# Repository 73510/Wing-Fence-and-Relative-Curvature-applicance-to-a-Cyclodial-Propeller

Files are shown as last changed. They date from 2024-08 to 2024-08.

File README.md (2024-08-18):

# Wing Fence and Relative Curvature applicance to a Cyclodial Propeller🚁
 사이클로디얼 프로펠러에 윙펜스와 상대 곡률 이론 적용시 일어나는 성능 변화를 실험적으로 검토했습니다.

## 📚 프로젝트 개요

이 저장소는 사이클로디얼 프로펠러의 성능을 개선하기 위한 연구를 담고 있습니다. 프로젝트는 여러 버전을 거쳐 발전했으며, 각 버전은 다양한 측면과 대회에 초점을 맞추었습니다.

## 🗂 저장소 구조

```
├─BUILD
│  ├─V0_V1_BUILD
│  └─V2_V3_BUILD
├─대회 출전 Documentation
│  ├─V0_교내과제연구
│  ├─V1_서울과학전람회예선
│  ├─V2_삼성휴먼테크논문대상
│  └─V3_KSEF CYC
└─데이터 및 실험 설계
    ├─Codes
    └─rawdata
```

## 🔬 연구 진행 과정

### V0: 교내 과제 연구
- Wing Fence와 Relative Curvature 개념 도입
- CFD(Computational Fluid Dynamics) 시뮬레이션 수행
#### 1차 모델 실험



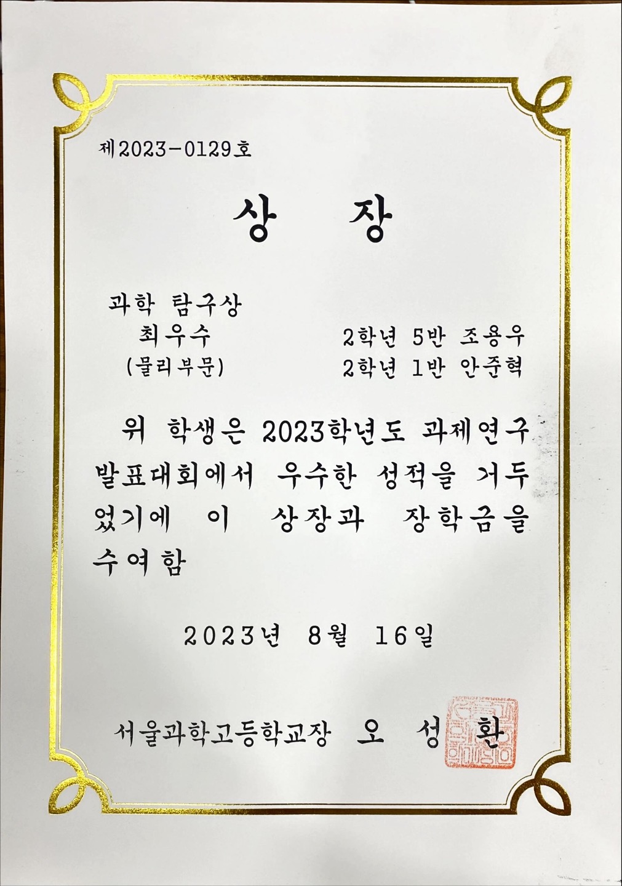
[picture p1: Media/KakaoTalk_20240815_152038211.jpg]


### V1: 서울과학전람회 예선 최우수상
- 프로펠러 설계 개선
- 논문 개선 및 수정



### V2: 삼성휴먼테크논문대상
- 최종 프로토타입 제작 및 성능 테스트
- Variable Pitcher 설계로 Pitch Distance 조절 가능
- 다양한 측정 도구를 활용한 종합적인 성능 분석 (RPM, 소음, 전력 소비량 등)

- 초록 통과, 본선 탈락
#### 2차 모델
- 기존의 3D 출력 날개가 무거워 폼보드 적용 경량화
- 부품 최소화시키고 프레임을 카본파이버로 구성
- 맞물린 기어 대신 풀리와 벨트 사용
- 하지만 폼보드 가공 문제에 부딫혀 3D 프린터로 만들게 됨

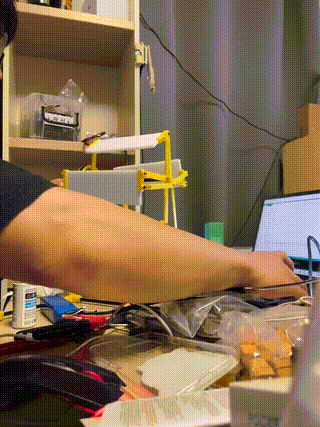
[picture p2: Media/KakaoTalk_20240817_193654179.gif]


#### 3차 모델
- NACA 0012 단면 형상 적용 날개
- Flaparm 내구도 문제 제외 완벽했다 -> 최종 모델에서 개선
- 2차 모델에 비하여 약간의 무게가 증가한 것이 단점

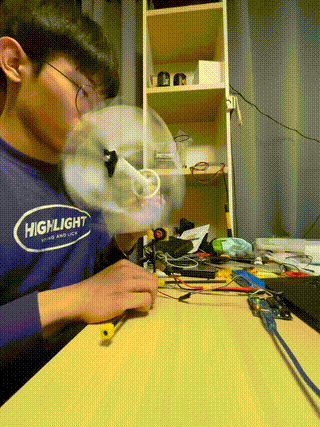
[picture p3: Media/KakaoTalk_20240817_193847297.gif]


#### 최종 모델 : 
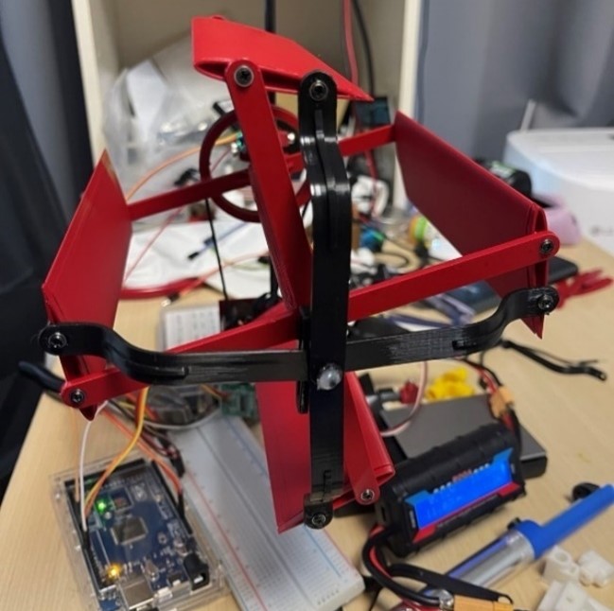
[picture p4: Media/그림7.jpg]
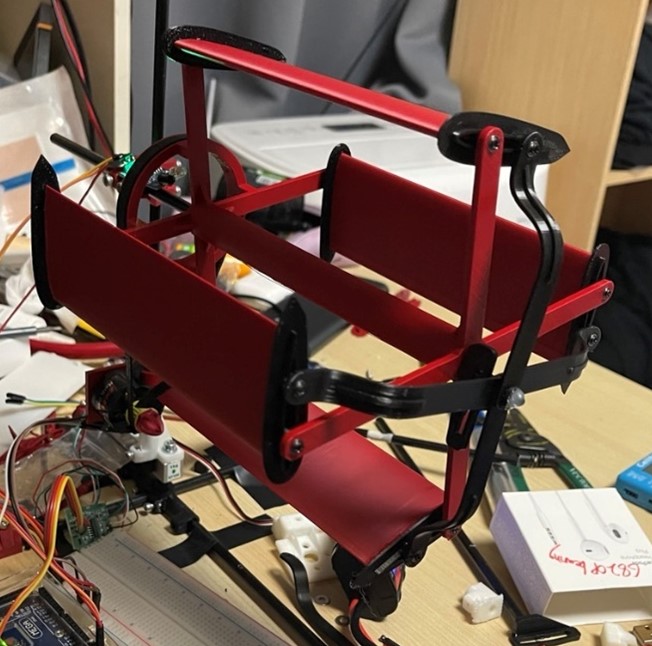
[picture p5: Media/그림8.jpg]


### V3: KSEF (Korea Science & Engineering Fair)
- 경량화 모델 LW-PLA 적용 실험
- 기존 프로펠러와의 성능 비교 분석
- 기존 프로펠러 실험 영상
  
  **Arduino Serial Monitor Loadcell & Tachometer RPM value**

- 최종 보고서 작성 및 개선

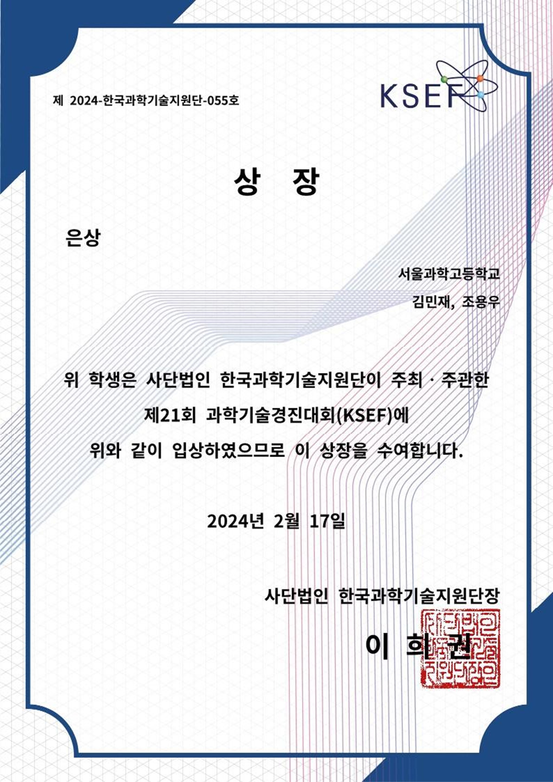
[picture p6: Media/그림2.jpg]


## 🛠 주요 연구 내용

1. [**프로펠러 설계 및 제작**](./BUILD/)
   - 3D 모델링 및 프린팅 (BUILD 폴더 참조)
   - 다양한 에어포일 설계 실험

2. [**성능 측정 및 분석**](./데이터%20및%20실험%20설계/)
   - Arduino를 이용한 데이터 수집
   - Python을 이용한 데이터 분석 및 시각화

3. [**Wing Fence 및 Relative Curvature 연구**](./대회%20출전%20Documentation/)
   - 이론적 배경 및 적용
   - 실험과 CFD를 통한 효과 검증

4. [**경량화 연구**](./대회%20출전%20Documentation/V3_KSEF%20CYC/)
   - LW PLA 활용 실험
   - 강성 유지와 경량화 사이의 균형점 모색

## 📊 데이터 및 결과

- 실험 원시 데이터: [`rawdata`](./데이터%20및%20실험%20설계/rawdata/) 폴더
- 데이터 분석 결과: [`데이터 및 실험 설계`](./데이터%20및%20실험%20설계/) 폴더
- 최종 연구 결과: [`대회 출전 Documentation/V3_KSEF CYC`](./대회%20출전%20Documentation/V3_KSEF%20CYC/) 폴더

## 🔮 향후 연구 방향

- 더욱 효율적인 에어포일 설계 탐구
- 다양한 소재를 활용한 경량화 연구 지속
- 실제 비행체 적용을 위한 스케일업 연구

## 📧 연락처

프로젝트에 대해 궁금한 점이 있으시면 언제든 연락 주세요!

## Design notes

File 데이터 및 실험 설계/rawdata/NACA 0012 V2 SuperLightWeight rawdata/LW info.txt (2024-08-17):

원래 PLA Not Curved WF Assemble

Main144 + L Wf + R WF + insert x3 = 17.4g

LightWeight Version -> 6.5g으로 경량화.

Setting
flowrate 0.4에 (0.41~0.42는 되야 함)Layer height 0.3, width 0.6에 Vase mode

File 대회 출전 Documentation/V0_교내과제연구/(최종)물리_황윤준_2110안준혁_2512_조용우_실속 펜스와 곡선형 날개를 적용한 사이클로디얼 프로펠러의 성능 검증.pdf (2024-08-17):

- 1 -

## 실속 펜스와 곡선형 날개를 적용한 사이클로디얼 프로펠러의 성능 검증

안준혁 ․ 조용우 ․ 황윤준
서울과학고등학교

### Wing Fence & Curved Wing Effect on Cyclodial Propellers

JunHyuk Ahn ․ Yongwoo Cho ․ Yunjun Hwang Seoul Science High School

### 국문 초록

본 연구에서는 Cycloidal Propeller의 효율 개선을 위해 Wing Fence 구조와 Virtual Camber 효과를 고려한 날개

형상을 적용하는 방안을 모색하였다. Cycloidal Propeller는 회전축이 유체의 이동 방향에 수직인 유체 추진 장치

로, 항공 및 수상 차량의 추진, 상승, 조종에 사용된다. 그러나 기존의 Cycloidal Propeller는 상대 곡률에 의해 전

력 손실이 발생하는 문제가 있었다. 이에 본 연구에서는 공력학적 장치인 Wing Fence의 원리를 도입하여 안정성

및 추력을 향상시키고, Relative Curvature 형상을 최적화하여 전력 손실을 줄이는 방안을 제시하였다. Computational Fluid Mechanics를 이용한 실험 결과, 새로운 구조와 형상이 적용된 Cycloidal Propeller는 기존 대

비 효율 개선을 보였으며, 이는 향후 항공 및 수상 차량의 추진 시스템에 대한 새로운 접근 방법을 제공할 것으로
기대된다. | Abstract

In this study, we tried to improve the efficiency of a cyclic propeller by applying a wing fence structure and a wing shape that considers the virtual camber effect. A cyclic propeller is a fluid propulsion device whose rotational axis is perpendicular to the direction of fluid movement, and is used for propulsion, ascent, and control of air and water vehicles. However, conventional cyclonic propellers suffer from power loss due to relative curvature. In this study, we propose to improve stability and thrust by introducing the principle of wing fence, an aerodynamic device, and to reduce power loss by optimizing the relative curvature shape. As a result of experiments using Computational Fluid Mechanics, the Cyclloidal Propeller with the new structure and shape showed efficiency improvement compared to the existing one, which is expected to provide a new approach to the propulsion system of air and water vehicles in the future.

Keywords : Cyclodial Propeller, Wing Fence, Virtual Camber, Computational Fluid Mechanics, 효율 개선

### I. 서론(Introduction)

Cycloidal Propeller는 유체 추진 장치로, 항공 및 수상 차량의 추진, 상승, 조종에 중요한 역할을 수행한다. 이러

한 기기의 효율을 극대화하기 위해 다양한 노력이 지속적으로 이루어지고 있다. 그러나 기존의 Cycloidal Propeller

는 상대 곡률로 인해 전력 손실이 발생하는 문제를 안고 있다. 이러한 문제를 해결하고 Cycloidal Propeller의 성능

을 향상시키기 위한 연구가 시급하다. 이에, 본 연구에서는 공력학적 장치인 Wing Fence 구조와 Relative

Curvature 형상을 Cycloidal Propeller에 적용, 그 성능 향상을 추구하는 것이 목표이다.

- 2 -

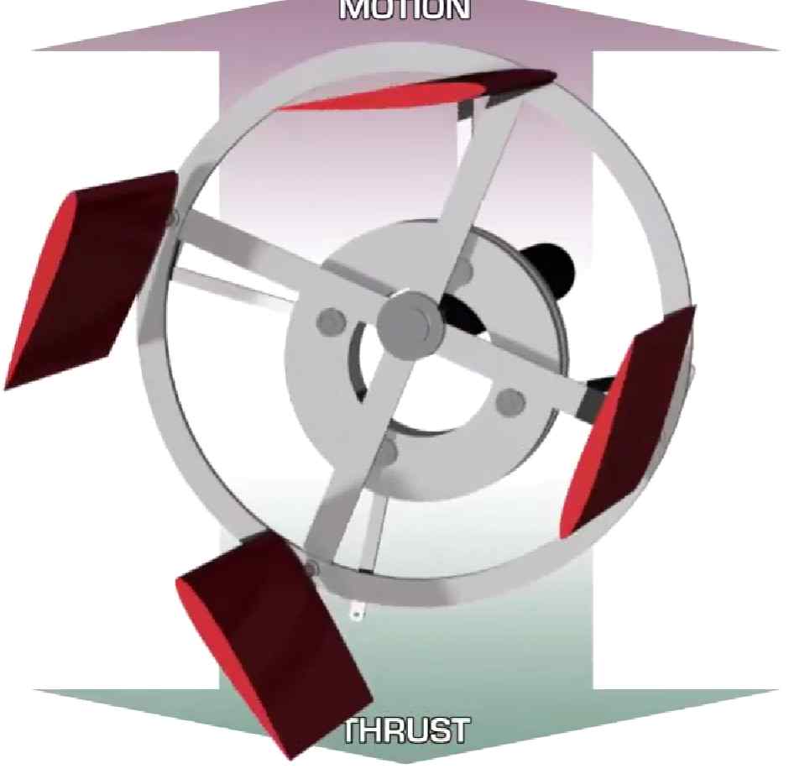
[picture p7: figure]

그림 1 : Cyclodial Propeller의 형상, 출처 https://youtu.be/Ub563Yc3xls. 축과 나란한 방향이 아닌, 축과 수직한 방향으로 추력이 발생하도록 회전한다. Flap이라는 구조가 회전하면서 추

력을 만들어내며, 기존 프로펠러와 달리 모든 면이 같은 속도로 공기와 만나 구조적으로 단순해진다는 장점이 존

재한다. Cycloidal Propeller와 관련된 이론과 선행 연구는 그 동작 원리와 구조, 그리고 성능 개선 방안 등에 집중되어

왔다. 특히, 이 장치의 추력 손실 문제를 해결하기 위한 다양한 접근법이 제시되었으나, 아직까지 뚜렷한 해결책은

마련되지 못하였다. 본 연구에서는 Wing Fence와 Relative Curvature라는 두 가지 새로운 개념을 도입한다. Wing Fence는 주로 스웹

트 날개(swept-wing) 항공기에 장착되며, 공기가 너무 멀리 이동하거나 속도가 빨라져 전체 날개가 한번에 기능을

상실하는 것을 방지하는 역할을 한다. 반면, Relative Curvature는 날개의 곡률을 조절하여 날개 주변의 유동을 최

적화하고 전력 손실을 줄이는 방식이다. 이 두 가지 개념을 Cycloidal Propeller에 적용하여 그 성능을 개선하고자

하는 것이 본 연구의 주요 동기이다. 스웹트 날개(swept-wing) 항공기가 저속으로 비행할 때, 날개의 전방 모서리 각도로 인해 일부 공기 흐름이 횡방향

으로, 즉 날개 끝쪽으로 이동하게 된다. 이 과정은 점진적으로 진행되며, 날개 중앙 부근의 공기 흐름은 전방 모서

리 각도뿐만 아니라 날개 뿌리로부터의 횡방향 공기 흐름에 영향을 받는다. 이로 인해 날개 끝에서는 공기 흐름이

거의 모두 횡방향으로 이동하게 되어, 이는 날개를 앞뒤로 가로지르는 흐름과 대조적이다. 이는 결과적으로 효과적

인 공기 속도가 크게 떨어져 날개가 고속 유동 상태에서 벗어나게 된다. 이런 문제를 해결하기 위해 'Wing Fence'의 도입이 필요하다. 'Wing Fence'는 공기 흐름이 너무 멀리 이동하거나

속도가 빨라져 전체 날개가 한번에 기능을 상실하는 것을 방지하는 역할을 한다. Cyclodial Propeller에서 또한, 날

개 양 끝단에서 발생하는 횡방향 모멘텀을 올바르게 제어하고 추진하기 위해서는 wing fence의 구조가 필요하다. 본 연구에서는 Cycloidal propeller의 성능 개선과 관련하여 다음 세 가설을 세우고, 이를 증명하기 위한 시뮬레

이션과 실험을 진행하였다. 가설 1. Cycloidal propeller의 회전 반경과 같은 곡률 반지름의 날개를 이용하면 drag를 감소시켜 효율을 높일

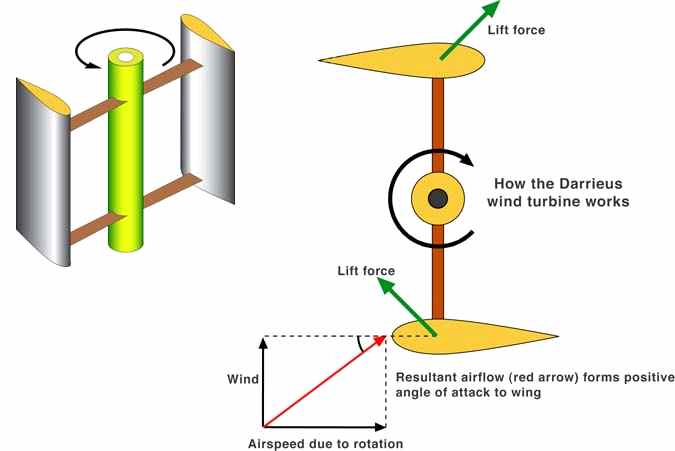
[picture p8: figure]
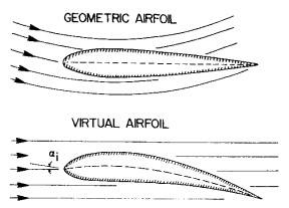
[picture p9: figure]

- 3 -

수 있다. 가설 2. Cycloidal propeller의 회전 반경과 같은 곡률 반지름의 날개를 이용하면 추력을 증가시킬 수 있다. 가설 3. Cycloidal propeller의 날개에 wing fence 구조를 설치하면 추력 개선 효과가 있다.

### II. 연구방법 및 이론(Method & Theory)

### 1. 가설에 대한 정성적인 근거

가설 1) P. G. Migliore의 ‘Flow Curvature Effects on Darrieus Turbine Blade Aerodynamics’에 따르면, Darrieus

turbine blade의 공기역학적 특성에는 유체 흐름의 곡률이 중요한 영향을 끼친다. Darrieus turbine은 cyclorotor와

마찬가지로 익형 구조의 날개를 어떤 축 주위로 회전할 수 있도록 하는 풍력 발전기이다. 이때 각각의 날개는 곡선

운동을 하게 되는데, 이 때문에 실제보다 캠버(camber)가 큰 (익형의 휘어진 정도가 큰) 효과가 발생한다고 한다. 이를 virtual camber effect라 한다. 해당 논문에서는 이를 conformal mapping technique를 이용하여 표현한다. 또

한 virtual camber effect의 conformal mapping을 나타낸 아래 그림에서 알 수 있듯 받음각(Angle of Attack, AoA)

이 증가하는 효과도 있다.

그림 2 : Darrieus turbine의 작동 원리

그림 3 : Curvilinear flow에 대해 conformal mapping

을 적용한 virtual airfoil 주의의 rectilinear flow

Cycloidal propeller의 회전 반경과 같은 곡률 반지름의 날개를 이용할 경우, 날개 주위의 유속이 rectilinear flow

의 모양을 따르도록 conformal mapping을 하면 angle of attack이 0인 상황과 대응되며, drag force가 최소이다. 따

라서 날개가 지면과 수직인 방향으로 이동할 때도 virtual camber effect에 의해 drag가 생성되는 편평한 날개에 비

해 곡률 반지름이 날개의 회전 반경과 일치하는 날개가 에너지 관점에서 더 효율적일 것이다.

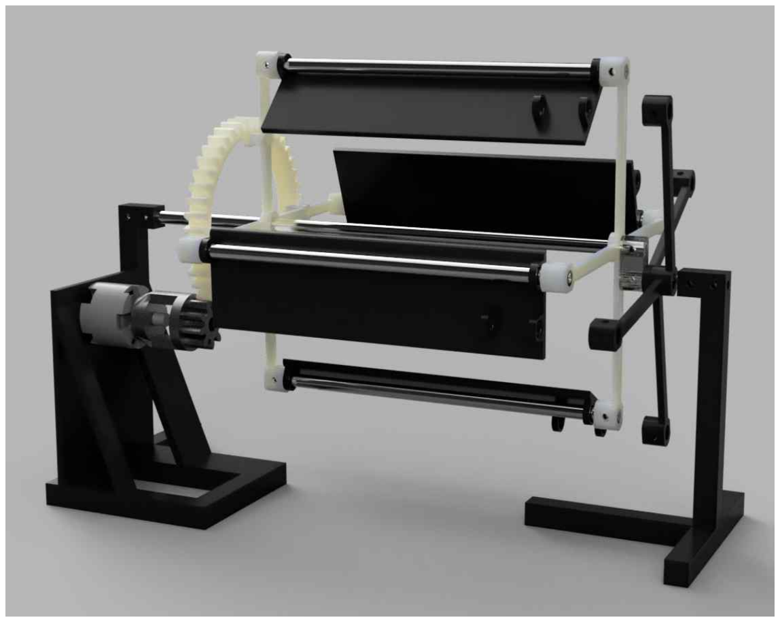
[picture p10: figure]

- 4 -

가설 2) 날개 자체가 휘어져 있으면 virtual camber effect 외에도 날개에 camber가 있는 효과가 있어 날개가

cycloidal propeller의 위, 아래쪽에 있을 때 받는 양력이 더 클 것이다. 가설 3) Swept-wing 항공기에 설치되는 wing fence와 마찬가지로, cycloidal propeller의 날개에 wing fence 유사

구조물을 설치하면 날개에 나란한 방향으로의 유체 흐름을 막아 날개에 수직한 방향의 운동량을 유지하는 효과가

있어 양력이 클 것이다.

2. 3D Printed Parts & Structure

연구를 진행하기 위해, Cyclodial Propeller를 3D 프린터로 만들었다. 이를 위해 아래 사진과 같이, 다양한 날개의 구조를 실험할 수 있는 Cyclodial Propeller를 제작하였다.

그림 4 : 전체 Cyclodial Propeller 실험 장치의 구성

다음은 각 부품에 대한 명칭 및 이름이다.

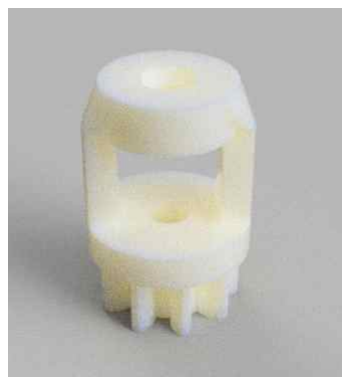
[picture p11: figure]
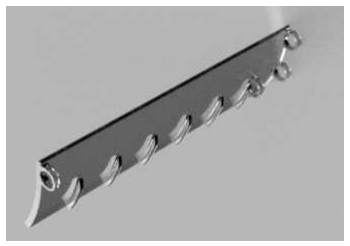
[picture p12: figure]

- 5 -

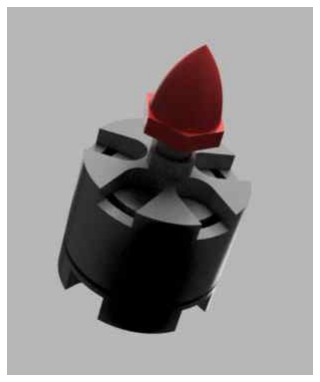
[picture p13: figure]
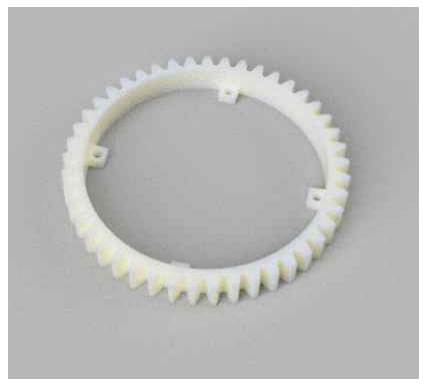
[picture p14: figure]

그림 5 : A : 45T Module 2 Gear. 큰 기어로 1/5의 비로 모터와 주회전축 로터를 연결한다. B : Real Gear 9. 모

터 마운트의 형상에 기초하여 모터에 쉽게 탈부착가능한 기어이다. 9T이다. 두 기어 모두 Fusion 360의 Spur Gear

를 사용했으며, 두께 10mm 에 Module 2로 설계하였다. C : MT2212 motor. 실험에 쓰이는 드론 모터로, 주로 멀

티콥터에 적용되는 모터이다. 프로토타입을 만들었을 때 2 : 1 의 비로 연결하였으나 작동하지 않아, 차후 5 : 1

의 기어비로 수정하였다.

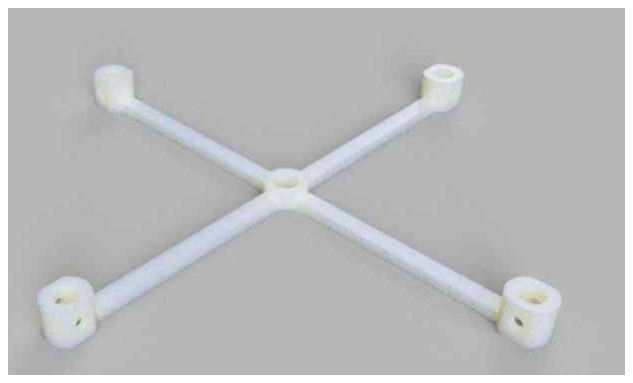
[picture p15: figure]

그림 6 : A : CenterArm. 주회전축의 날개 4개가 회전하는 것을 붙잡는 중앙 지지대이다. B : CenterArmGear.

기어를 마운트할 수 있는 스페이서와 구멍이 연결되어 있어 나사로 연결 할 수 있다. 마찬가지로, 주회전축의 날

개 4개 회전을 붙잡는 중앙 지지대이다. C : FlapArm. 날개의 각도가 유동적으로 제어되는데 있어 필수적인, 이

심축에 연결되어 날개의 각도를 제어하는 지지대이다. 이때, 각 Arm 사이에는 내경 4mm 외경 6mm 알루미늄

파이프로 연결된다. D : Pitch12mm. 이심축과 주회전축을 연결하는 연결 부위이다. 12mm의 간격을 두고 떨어

져 있다.

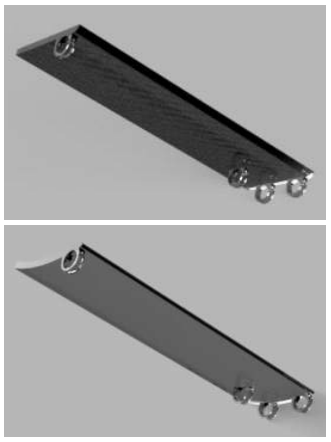
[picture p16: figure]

그림 8 : A : StraightFlap. B : StraightWF Flap. C : RoundFlap. D : RoundWF Flap.

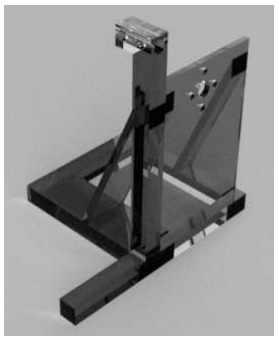
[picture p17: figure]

- 6 -

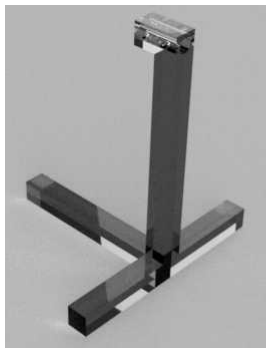
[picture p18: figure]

그림 9 : A : Stand. 회전축을 고정하기 위한 스탠드이다. 이심축이 두 개의 나사로 고정된다. B : StandMotorMount. 모터

마운트와 지지대가 포함된 스탠드이다. 모든 설계 자료는 “설계 자료” directory에 fusion 360 archive 형식으로 저장되어 있다.

### 3. 파이썬을 이용한 Flap Angle Distribution 찾기

Flap의 각도는 주회전축과 이심축 사이 거리, 날개의 반지름, Flap고정축간 거리에 의해 결정된다. 하지만 이 관

계가 비선형적이기 때문에, 파이썬을 이용해 각도 분배를 찾았다. 아래는 이를 찾기 위한 좌표평면상 좌표 정의이다.

- 7 -

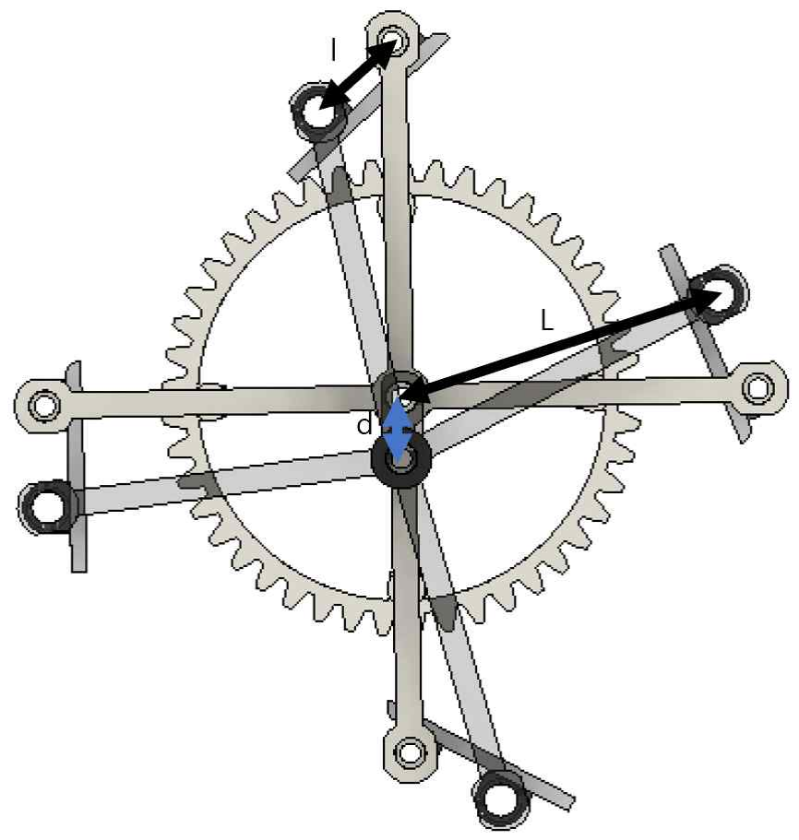
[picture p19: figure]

그림 10 : 회전축에 수직한 면에서 바라본 구조이다. l : Flap에서 두 고정축 간 거리 (두 축은 회전 가능함). 20mm로 설계되었다. L : 주회전축과 Flap이 고정되는 축 사이 거리. CenterArm과 FlapArm 모두 70mm 길이로 설계되었다. d : 주회전축과 이심축 간 거리, 본 설계에서는 12mm이다. Pitch Angle : Flap이 주회전축을 중심으로 하며 반지름이 L인 원의 접선과 이루는 각도. Theta : 좌표평면상 회전각, 0부터 2까지의 값을 가진다. 그래프에서는 x축이며, 편의를 위해 0~2까지의 값으로

scale down 하였다. 다음과 같이 값과 좌표를 설정한 이후, 파이썬을 이용한 수치대입법으로 해를 근사하여 구한 이후, 각도를 계산하

여 그래프를 그렸다. (첨부폴더 mechanicspy)

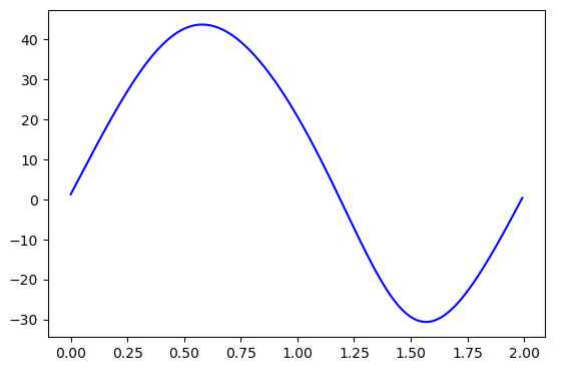
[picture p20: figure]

그림 11 : 그래프 y축은 도, x축은 theta/이다. A : d : 12mm, L : 70mm, l : 20mm의 설계. 최종 설계 버전의

각도 분배이며, 최댓값 43.7도, 최솟값 –30.6도의 값을 가진다. B : d : 10mm, L : 80mm, l : 20mm. 초기 설계이

며, 최댓값 36.4도, 최솟값 –24.0도의 값을 가진다. L의 증가는 최대각과 최소각의 절댓값 차이를 줄이는 역할을 하며, 위아래의 출력을 더 편평하게 맞추는데 기여

한다. d의 증가는 더 큰 Pitch Angle을 준다.

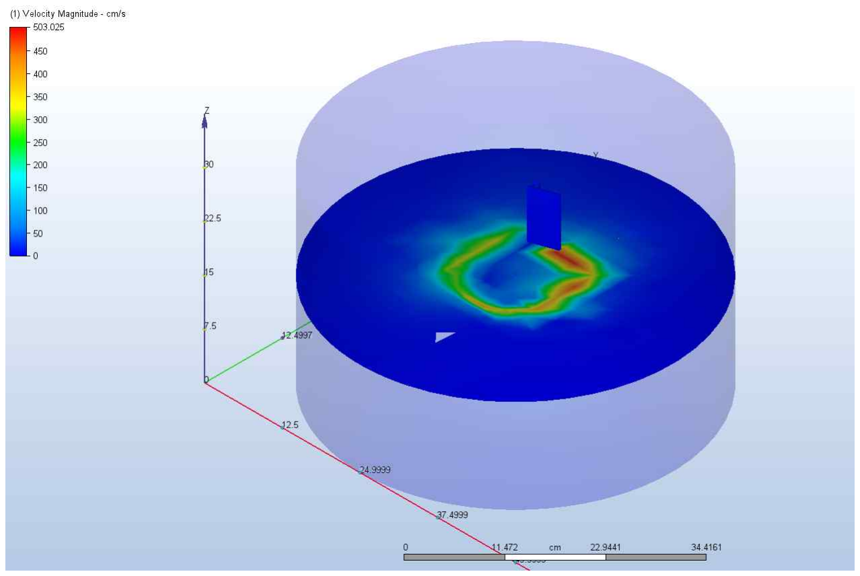
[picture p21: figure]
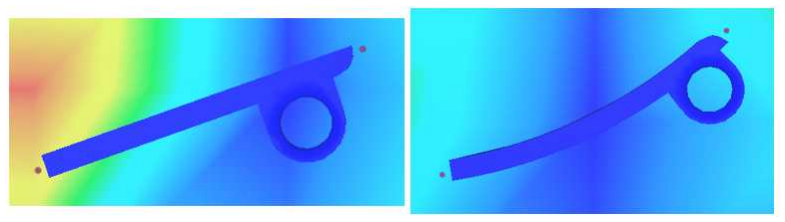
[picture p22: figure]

- 8 -

### 4. CFD 시뮬레이션을 이용한 가설 1 검증

Cycloidal propeller의 날개 구조에 따라 pitch angle이 0일 때 작용하는 drag force를 비교하기 위해 Autodesk

CFD를 이용한 시뮬레이션을 진행했다. 실제 실험 조건과 같이 지름 500mm인 영역의 중심을 기준으로 반지름

70mm인 원형 궤도를 따라 StraightFlap 또는 RoundFlap을 700 RPM으로 회전시켰다. 유체는 Air, 날개는

ABS(molded)로 설정했다.

그림 12 : StraightFlap 회전 시뮬레이션 이미지

총 100 step 동안 시뮬레이션을 작동시켰으며, 91~100 step에서 날개의 중심을 수직으로 관통하는 평면에서 아래

그림과 같이 날개의 진행방향을 기준으로 앞과 뒤 점의 압력을 측정했다.

그림 13 : A. StraightFlap 앞뒤 압력 측정점 / B. RoundFlap 앞뒤 압력 측정점

### 5. CFD 시뮬레이션을 이용한 가설 3 검증

Cycloidal propeller의 날개에 부착된 wing fence 구조의 효과를 이론적으로 확인해보기 위해 Autodesk CFD를

이용한 시뮬레이션을 진행했다. 10m/s의 rectilinear한 공기 흐름 속에서 StraightFlap과 StraightWF Flap을 각각

pitch angle이 0도, 15도인 경우에 대해 50 step 이후의 결과를 측정했다. 시뮬레이션 영역은 날개를 중심에 둔

300mm*200mm*500mm 크기의 직육면체이다. 유체는 Air, 날개는 ABS(molded)로 설정했다.

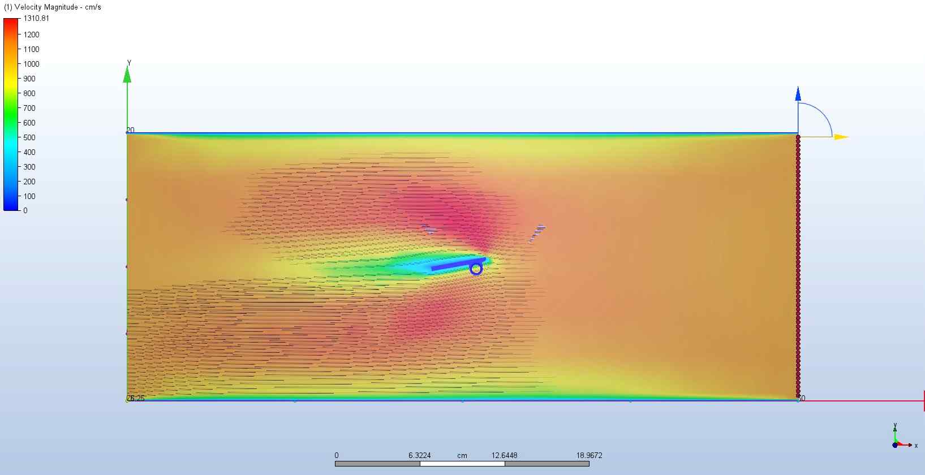
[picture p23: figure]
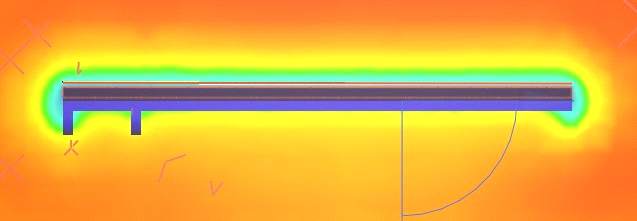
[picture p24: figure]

- 9 -

그림 14 : Pitch angle 이 15도인 StraightFlap 주위의 유체 흐름 단면도

50 step 정도에 공기의 흐름이 평형상태에 도달했다고 가정하고 날개를 관통하며 공기 흐름에 수직한 방향으로

자른 평면상에서 날개의 바로 위쪽의 직선을 따라 공기의 속력을 측정했다. 또한 이때 날개에 작용하는 x, y, z 방

향 힘을 측정했다.

그림 15 : 날개 위 속력이 비취색으로 표현된 영역의 붉은색 가로줄을 따라 속력 데이터를 측정했다.

6. 1차 실험

3D 프린터와 레이저 커터를 이용하여 부품을 출력한 후 아래 그림과 같이 1차 실험에 사용한 모델에 맞게 조립

하였다. 기존 설계상으로는 드론 모터를 이용하여 cycloidal propeller를 회전시키려 했으나 해당 설계상 기어비가

낮아 모터의 토크가 충분하지 않았다. 따라서 1차 실험에서는 드릴에 기어를 부착해 cycloidal propeller를 작동시켰

다. 회전 각속도를 알기 위해 타코미터를 사용했다. 아래 그림의 B와 같이 모델의 받침대 부분을 Force Plate 위에

고정시키고 Vernier Labquest를 이용하여 시간에 따른 힘 데이터를 측정했다. Cycloidal propeller를 Force Plate 위

에 설치하기 전에 Vernier Labquest로 영점 조절을 해야 한다.

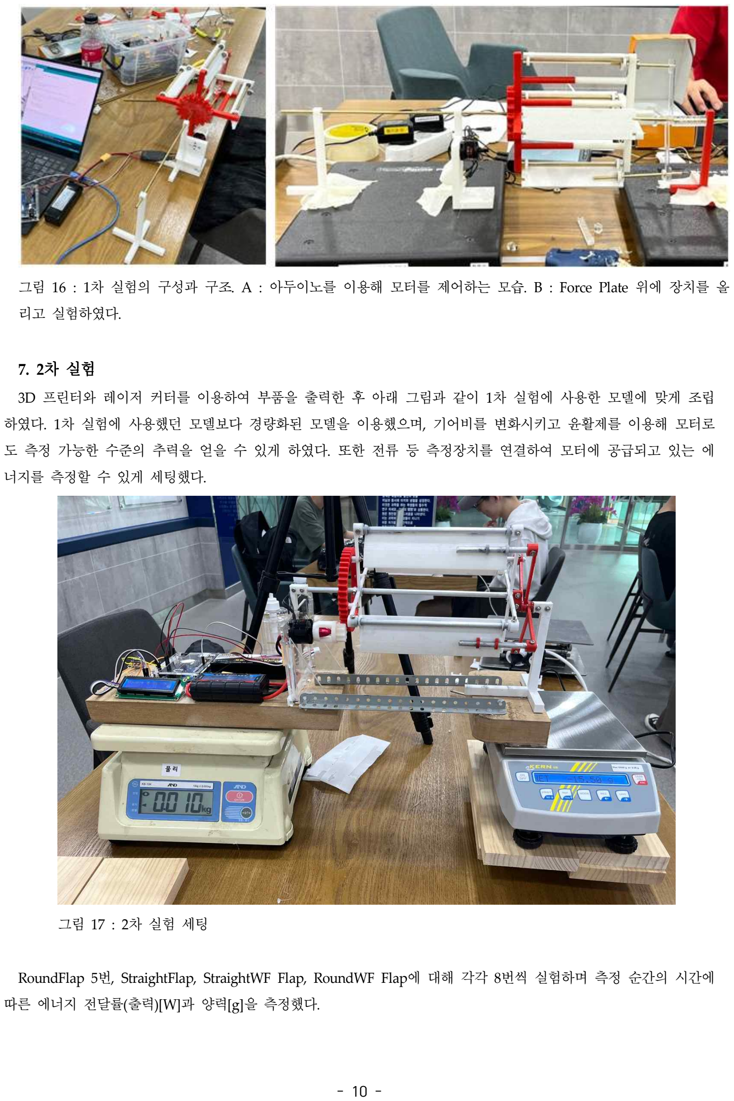
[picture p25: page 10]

- 10 -

그림 16 : 1차 실험의 구성과 구조. A : 아두이노를 이용해 모터를 제어하는 모습. B : Force Plate 위에 장치를 올

리고 실험하였다.

7. 2차 실험

3D 프린터와 레이저 커터를 이용하여 부품을 출력한 후 아래 그림과 같이 1차 실험에 사용한 모델에 맞게 조립

하였다. 1차 실험에 사용했던 모델보다 경량화된 모델을 이용했으며, 기어비를 변화시키고 윤활제를 이용해 모터로

도 측정 가능한 수준의 추력을 얻을 수 있게 하였다. 또한 전류 등 측정장치를 연결하여 모터에 공급되고 있는 에

너지를 측정할 수 있게 세팅했다.

그림 17 : 2차 실험 세팅

RoundFlap 5번, StraightFlap, StraightWF Flap, RoundWF Flap에 대해 각각 8번씩 실험하며 측정 순간의 시간에

따른 에너지 전달률(출력)[W]과 양력[g]을 측정했다.

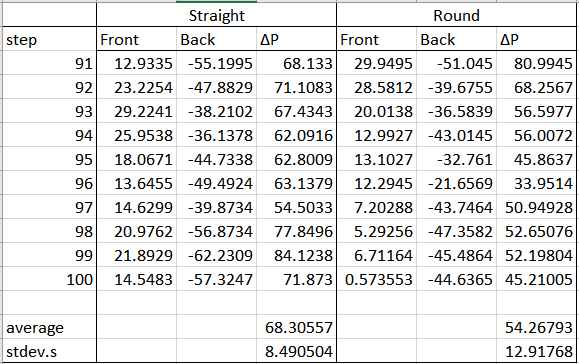
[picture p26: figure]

- 11 -

### III. 결과

### 1. 시뮬레이션 – 가설 1

다음 표는 91~100 step 범위에서의 StraightFlap, RoundFlap 앞뒤 압력 데이터이다. 시간, 공간 간격이 완벽히 연

속적이지 않아 압력 값이 많이 바뀌므로 10개 step에 대한 앞뒤 압력차의 평균을 구했다. 단위는 dyne/cm^2이다. 두 날개에 작용하는 drag force는 이 압력차에 비례한다고 근사할 수 있다. 아래 표에서 확인할 수 있듯이

StraightFlap보다 RoundFlap에서 압력차가 더 작다. 즉, pitch angle이 0일 때 RoundFlap이 받는 drag force가

StraightFlap이 받는 drag force보다 작을 것이라 유추할 수 있다.

표 2 : 시뮬레이션 결과. 단위는 dyne/cm^2이다.

### 2. 시뮬레이션 – 가설 3

다음 표는 날개 방향과 나란하며 날개 면과 가까이 있는 선분 위에서 측정한 날개 방향의 속도 분포에 대한 평

균과 표준편차 데이터이다. Model 중 ‘NF’는 wing fence 구조가 없는 것, ‘WF’는 wing fence 구조가 있는 것을 의

미한다. ‘Normalized’ 열은 속도 분포를 정규화한 것인데, 서로 다른 실험 환경에서의 데이터를 비교하기 위해 속력

이 최대인 것을 1로 맞추도록 하여 일정한 비율로 속도 데이터를 변화시킨 데이터이다.

표 3 : 시뮬레이션 결과. 단위는 cm/s이다. 아래는 pitch angle이 0도일 때 wing fence 구조가 있는 모델과 없는 모델에 대해 정규화한 속도 데이터를 각각

그래프로 나타낸 것이다. Wing fence 구조가 없을 때는 속도가 거의 단조 증가하나, wing fence 구조가 있을 때는

그 주위에서 속력 분포가 0 주위로 진동하는 것을 알 수 있다. 그 결과 평균적인 날개 방향의 유체 흐름이 더 적

고, 표준편차도 작다.

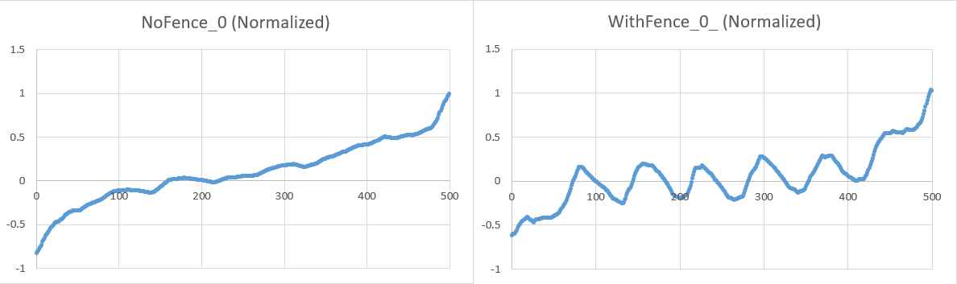
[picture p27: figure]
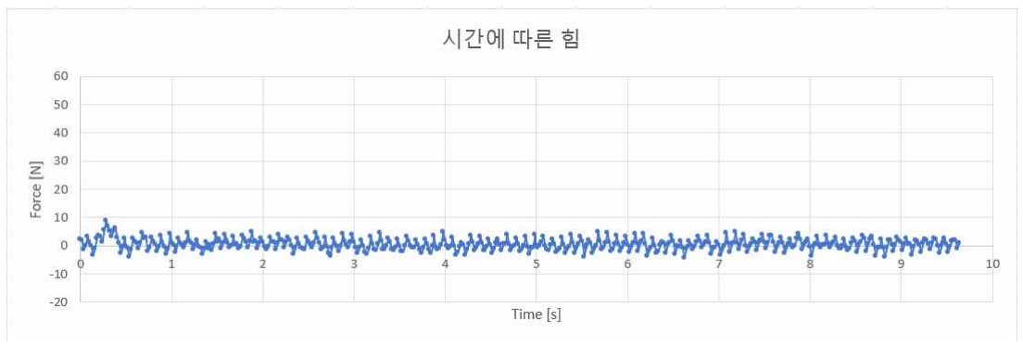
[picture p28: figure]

- 12 -

그림 18 : Wing fence 구조가 있을 때와 없을 때 정규화된 속도 분포 그래프. 단위는 cm/s이다. 한편 이때 날개에 작용하는 양력과 drag를 계산해보았다. Pitch angle이 0도일 때보다 15도일 때 전반적으로 큰

양력이 작용한다. 같은 pitch angle에 대해 pitch angle이 0도일 때는 wing fence 구조가 없을 때보다 있을 때 양력

이 매우 크지만, 15도일 때는 양력이 조금 감소했다. 한편 drag의 경우 두 경우 모두 wing fence 구조가 있을 때

drag force가 작다.

표 4 : Pitch angle과 wing fence 구조 존재 여부에 따

른 drag와 양력. 단위는 dyne이다.

3. 1차 실험 결과

실험 시간이 충분하지 않아 1차 실험은 총 2번만 진행할 수 있었다. 첫 번째 실험에서는 650.3 RPM ~ 683.3

RPM 범위에서 평균적으로 666.7 RPM으로 기어가 회전하는 상태에서 Force Plate에 작용하는 힘을 측정했다. 값이

0N 주위에서 진동하는 무의미한 결과를 얻었다.

두 번째 실험에서는 374.4 RPM ~ 1040.9 RPM 범위에서 평균적으로 약 710.4 RPM으로 기어가 회전하는 상태에

서 Force Plate에 작용하는 힘을 측정했다. 마찬가지로 유의미한 결과를 얻지 못했다.

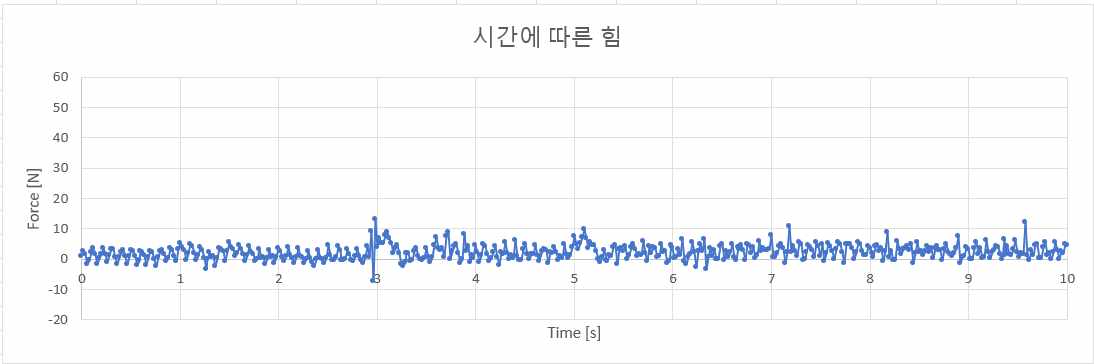
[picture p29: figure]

- 13 -
4. 2차 실험 결과

각각의 날개에 대한 출력과 양력 데이터를 이용하여 출력에 따른 추력 그래프를 그리고 선형회귀를 진행했다. 출

력이 0일 때 발생할 수 있는 양력은 0이므로 y절편 또한 0으로 고정했다. 양력이 L, 출력을 P라 하고 두 변수 사이

에 선형 관계가 성립한다고 가정하면 이는 기울기 A에 대해 라는 식으로 표현할 수 있다. 기울기 A가 클

수록 같은 출력으로 더 큰 양력을 발생시킬 수 있으므로 효율이 좋은 조건이다. 각각의 날개에 대해 기울기를 비교

하여 효율을 비교했다.

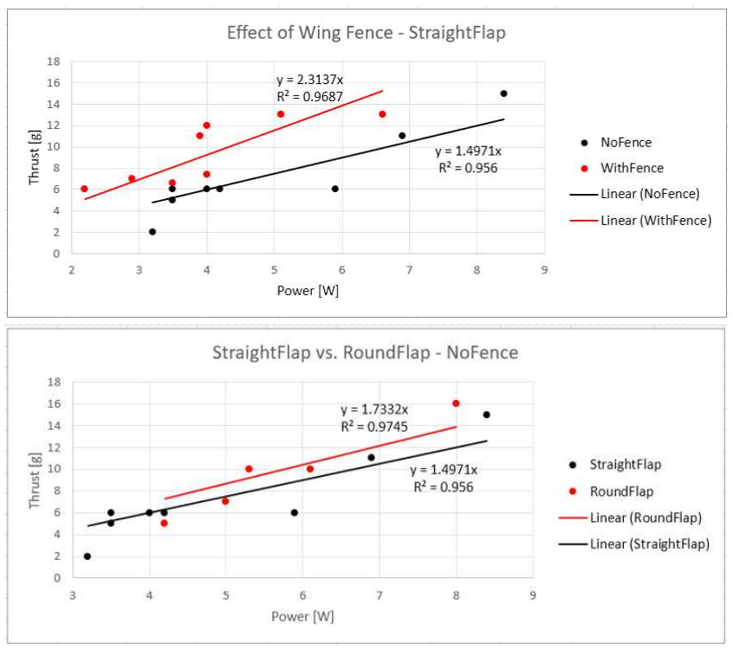
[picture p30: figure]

- 14 -

그림 21 : 2차 실험 결과이다. StraightFlap 보다 RoundFlap의 성능이 15.77% 증가한 것을 알 수 있다. Wing Fence의 경우 성능을 늘린다는 것

을 StraightFlap에 한정해서 검토하였다. StraightFlap에 WingFence를 적용한 것은 54.55%나 성능이 증가한 것을

확인했다. RoundFlap에 대한 성능 검증은 시간 부족으로 진행하지 못했다.

### IV. 고찰 (Discussion)

1. 1차 실험의 문제점

1차 실험에서는 유의미한 결과를 얻을 수 없었다. 이에 대해 크게 두 가지 이유가 존재한다고 예상된다. 첫째로, 모터의 추력에 비해 과도한 회전관성과 마찰로 인해 회전체가 잘 회전하지 않았다. 그뿐만 아니라 내부적인 간섭

및 진동이 심했으며 경량화 되지 않은 수많은 구조들로 인해 불필요한 에너지 소모가 많았다. 조립에 있어서도 편

리하지 못했으며 전체적으로 질이 낮았다. 이러한 점을 모두 고쳐 2차 설계를 진행했다. 이 문제들을 개선하기 위해 2차 실험에 사용할 모델을 다시 설계했다. II. 연구방법 및 이론에 제시된 모델이 2차

실험에 사용할 설계이다. 첫째로, 기어비를 2:1에서 5:1로 변경하였으며, 전체적인 부피를 줄여 경량화를 이루었으며, 신주봉 대신 알루미늄 봉으로 교체하여 더욱 더 경량화 시켰다. 신주봉의 밀도가 8.3

이고, 알루미늄의 밀도가

2.7

, PLA infill 50%의 밀도가 0.7

이라고 가정하고 계산한 결과, 초기 모델의 회전체 무게만 해서 총

330.5g이 나왔다.

- 15 -

3D 구조물 207g, 베어링 31.2g (604zz 모델의 베어링, 총 12개, 개당 2.6g), 신주봉 92.3g ((16 + 6) *4cm 가 쓰였다

고 가정, 두께는 4mm)

토탈 330.5g

이후 설계에서는 다양한 부분에서 무게를 덜어, 114g으로 무게를 줄일 수 있게 되었다.

3D 구조물 76.93g 알루미늄 37.3g 총 114g

### 2. 가설 1의 검증

개선한 cycloidal propeller를 이용한 2차 실험을 통해 곡률 반지름이 회전 반경과 같은 날개를 이용했을 때 양력

이 향상하는지를 확인할 수 있으며, wing fence의 영향은 시뮬레이션을 통해 이론적으로 확인했다. 그러나 해당 곡

률 반지름의 날개를 사용했을 때의 drag 감소만을 독립적으로 실험하기는 어려워 시뮬레이션으로 확인해야 할 것

이라 판단된다. 연구 중 곡률 반지름이 회전 반경과 같은 날개를 이용하면 virtual flow 관점에서 drag가 감소한다

는 가설 1을 검증하기 위해 시뮬레이션을 시도해 보았으나, 속력이 발산하는 등의 오류가 발생했다. 추후 다른 시

뮬레이션 방법을 시도하여 가설 1을 이론적으로 검증해볼 계획이다. 추가적인 실험 수행시, 특정 RPM에 도달하기 위한 전류량을 측정하는 등의 방식으로 회전에 소요되는 Drag을

측정할 수 있을 것이다. 즉, 전류량과 RPM, 추력의 관계에 대한 그래프를 그리고, 그로부터 상관계수를 정의하여

Drag을 추정할 수 있을 것이다. | V. 결론(Conclusion)

가설 1. Cycloidal propeller의 회전 반경과 같은 곡률 반지름의 날개를 이용하면 drag를 감소시켜 효율을 높일

수 있다. RoundFlap을 이용한 날개의 경우, StraightFlap을 적용한 날개에 비해서 15.77% 성능 증가가 있었다. 이는 앞서

제시한 유선형 저항 감소의 원인으로 파악된다. 가설 2. Cycloidal propeller의 회전 반경과 같은 곡률 반지름의 날개를 이용하면 추력을 증가시킬 수 있다. RoundFlap을 이용한 날개의 경우, StraightFlap을 적용한 날개에 비해서 15.77% 성능 증가가 있었으며, 이는 앞

서 제시한 Pitch Angle의 증가로 인한 것으로 예상된다. 가설 3. Cycloidal propeller의 날개에 wing fence 구조를 설치하면 추력 개선 효과가 있다. Wing fence 구조가 있을 때와 없을 때 날개에 작용하는 양력, drag force, 날개 표면에서 날개와 나란한 방향으

로 흐르는 속력 분포를 시뮬레이션으로 분석한 결과, wing fence 구조가 있을 때 날개와 나란한 방향의 속력 성분

의 분포가 0에 더 가까우며 밀집되어 있고, 양력 또한 증가함을 확인했다. 즉 가설 3은 참이다. 시뮬레이션 뿐만 아

니라 실험적으로도 검증되었다. StraightFlap 보다 wing fence를 적용한 straightflap을 사용하였을 때 54.55%의 성능

증가가 있었다. 위에서 언급된 성능은, 모터에 공급되는 W로 발생하는 추력을 나눈 것을 성능효율 지표로 사용하였다.

- 16 -

### VI. 제언(Proposal)

현재 연구를 진행하면서, 저울로 구성한 실험장치의 진동으로 인해 측정의 안정성이 떨어진다는 것을 몸소 느꼈

다. 차후 연구에는 더욱 연구의 신뢰도를 높힐 수 있도록 Load Cell을 구비하여 구간 평균을 이용해서 실험장치의

진동에도 불구 더 안정적인 실험장치를 구성하고자 한다. 또한, PLA 필라멘트의 내구도 한계와 정확도, 알루미늄

봉 가공의 오차로 인해 발생하는 진동을 처리하기 힘들었다. 무게 감소를 위해 베어링을 제거하였으나, 베어링 제

거로 인한 마찰, 소음, 불안정성을 고려해보았을 때, 두 가지의 실험을 모두 진행해야 한다. 그뿐만이 아닌, 빠른 회

전으로 인한 부품의 팽창 및 휨으로 인해, Pitch Angle 및 로터 반지름의 증가 영향 또한 고려해야 할 것이며, RPM에 따른 추력 곡선을 훨씬 더 많으며 정밀한 데이터로 분석하여 이러한 형태의 로터를 어떠한 방식으로 적용

해야 할 것인지 찾아야 한다. 이러한 복잡한 로터의 구조는, 물론 기계적으로 최소한 단순화 및 경량화 시킨 구조임에도 불구하고 결과적으로

유지보수성과 내구성의 큰 손실을 야기한다. 이러한 점을 타파하고 더 넓은 적용처를 가지게 하기 위해, 이러한 결

함을 해결 및 보완할 수 있는 설계적 해결책 또한 차후 연구로 진행해보고 싶다. 현재 Flap의 구조는 납작한 평판 모양이지만, 이러한 평판 구조가 아닌, 실제 비행체에 적용되는 NACA Airfoil

의 구조를, 익형의 시위(중심선)가 Conformal Mapping의 경로 하여 회전체의 이동에 걸맞게 변형한 구조를 적용하

여 성능의 증가를 확인하고 싶다. 이러한 직접 만든 로터를 활용 개선하고, Carbon Fiber 및 다양한 경량 소재를 적용하여 사용가능한 드론을 개발

하고 싶다. 이러한 드론에 대한 특성을 연구하고 다양한 적용처를 알아보고 싶다. VII. 참고 문헌(Reference)

[1] "NACA Airfoil." Wikipedia, https://en.wikipedia.org/wiki/NACA_airfoil. Accessed 9 July 2023.
[2] P. G. Migliore, W. P. Wolfe and J. B. Fanucci, Flow Curvature Effects on Darrieus Turbine Blade

Aerodynamics, Published Online:23 May 2012, pp 49-55

[3] Hiromichi Akimoto, Yutaka Hara, Takafumi Kawamura, Takuju Nakamura and Yeon-Seung Lee, A

conformal mapping technique to correlate the rotating flow around a wing section of vertical axis wind turbine

and an equivalent linear flow around a static wing, Published 25 November 2013 • © 2013 IOP Publishing Ltd,

pp 1-10

### 보충 자료(Supplemental Information)

[1] FlapAngleDistribution
[2] 설계 자료

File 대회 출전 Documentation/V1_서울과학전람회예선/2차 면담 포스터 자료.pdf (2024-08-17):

# Wing Fence와 곡선형 날개를 적용한 사이클로디얼 프로펠러의 성능 검증

## 고교부 - 물리

### 1. 탐구(연구) 동기

제가 드론을 처음 보았을 때, 저는 신기하면서도 두려웠습니다. 드론 날개의 소음 때문에 불쾌했고, 두려웠지만 동시에 미래를

느꼈습니다. 프로펠러의 소음 문제 해결 없이는 이러한 드론을 저희 삶에 더 가까이 접목하기는 쉽지 않을 것입니다. 저희의 목적은 저소음, 저전력 프로펠러인 Cyclodial Propeller(일명

Voith Schneider propeller)의 성능을 개선하는 것입니다. 비행기 날개에 사용되는 구조인 Wing Fence 구조와, 회전하는

날개의 상대적인 곡률을 고려하는 Relative Curvature 이론을 접목하여 성능 개선을 이룰 수 있습니다. 2. 탐구(연구) 내용

가. 선행 연구 고찰 및 탐구의 독창성
Cyclodial Propeller :

Cyclodial Propeller는 회전축과 날개의 축이 평행하여 회전하면서 날개의 각이 변해 추력을 발생시키는 프로펠러이다. Relative Curvature : 곡선 운동을 하게 되는 날개에 대해, 공기에

대한 날개의 상대적인 움직임을 변환하는 Conformal Mapping Technique을 제안한 연구, P. G. Migliore의 ‘Flow Curvature Effects on Darrieus Turbine Blade Aerodynamics’를
참고하였다. 회전하는 상태에서 Cyclodial Propeller의 날개는 원형 경로를 따라 운동하기에 이러한 분석이 필수적이다.


Wing Fence : Swept-Wing 항공기에 설치되는 Wing Fence의 구조를 차용하였다. Wing Fence는 Wingtip Vortice의 감소로 인한 Lift Coeffcient 증가, Lift to Drag Ratio 증가, Stall Angle와 Effective AoA의 증가 효과를 가져다 준다.

다. 작품의 주요 내용

[A - 1] : 파이썬을 이용한 Flap Angle Distribution 찾기 [A - 2] : Cyclodial Propeller 3D 모델링 이후 조립


[A - 3] : Cyclodial Propeller 날개 구조별 추력 테스트
[B - 가설 1 검증] : CFD를 이용한 날개에 가해지는 Drag 비교 실험 [C – 가설 3 검증] : CFD를 이용한 날개로 얻어지는 추력 비교 실험 상기 구조들을 Cyclodial Propeller에 맞는 목적으로 해석하여 접목하기로 결정하였다.

나. 탐구 절차 및 방법

가설 1, Relative Curvature 1 : Cycloidal propeller의 회전 반경과 같은 곡률 반지름의 날개를 이용하면 Drag이 감소한다. 가설 2, Relative Curvature 2 : Cycloidal propeller의 회전 반경과

같은 곡률 반지름의 날개를 이용하면 추력을 증가한다. 가설 3. Wing Fence : Cycloidal propeller의 날개에 wing fence

구조를 설치하면 추력 개선 효과가 있다.

### 3. 탐구(연구) 결과

가설 1.
RoundFlap을 이용한 날개의 경우, StraightFlap을 적용한 날개에 비해서 15.77% 성능 증가가 있었다. 이는 앞서 제시한 유선형 저항 감소의 원인으로 파악된다. 가설 2.

RoundFlap을 이용한 날개의 경우, StraightFlap을 적용한 날개에 비해서 15.77% 성능 증가가 있었으며, 이는 앞서 제시한 Pitch Angle의 증가로 인한 것으로 예상된다. 가설 3.

실험적으로 StraightFlap 보다 Wing fence를 적용한 Straightflap을 사용하였을 때 54.55%의 성능 증가가 있었다. 이는 선행 연구들에서 밝혀졌듯, Rectinlinear Flow에서의 성능 증가 요인이 Cyclodial Propeller의 움직임에서도 그대로 적용되기 때문일 것으로 예상된다.

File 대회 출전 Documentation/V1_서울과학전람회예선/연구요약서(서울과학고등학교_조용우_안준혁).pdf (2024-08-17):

제65회 서울과학전람회 예선대회 작품요약서 | ※ 출품번호
출품부문 | 작 품 명
물리 | Wing Fence와 곡선형 날개를 적용한 사이클로디얼 프로펠러의 성능 검증

과학전시관에서 기재함

1. 탐구(연구) 동기


제가 드론을 처음 보았을 때 느낀 감정은, 신기하면서도
두려웠습니다. 드론 날개의 소음 때문에 불쾌했고, 두려웠 지만 동시에 미래를 느꼈습니다. 프로펠러의 소음 문제 해 결 없이는 이러한 드론을 저희 삶에 더 가까이 접목하기는 쉽지 않을 것입니다.
저희의 목적은 저소음, 저전력 프로펠러인 Cyclodial Propeller의 성능을 개선하는 것입니다.
비행기 날개에 사용되는 구조인 Wing Fence 구조와, 회전 하는 날개의 상대적인 곡률을 고려하는 Relative Curvature 이론을 접목하여 성능 개선을 이룰 수 있습니 다.
2. 탐구(연구) 내용
가. 선행 연구 고찰 및 탐구의 독창성
Relative Curvature : 곡선 운동을 하게 되는 날개에 대해, 공기에 대한 날개의 상대적인 움직임 을 변환하는 Conformal Mapping Technique을 제안한 연구, P. G. Migliore의 ‘Flow Curvature Effects on Darrieus Turbine Blade Aerodynamics’를 참고하였다.
Wing Fence : Swept-Wing 항공기에 설치되는 Wing Fence의 구조를 차용하였다.
상기 구조들을 Cyclodial Propeller에 맞는 목적으로 해석하여 접목하기로 결정하였다.
나. 탐구 절차 및 방법
가설 1. Cycloidal propeller의 회전 반경과 같은 곡률 반지름의 날개를 이용하면 Drag이 감소한다. 가설 2. Cycloidal propeller의 회전 반경과 같은 곡률 반지름의 날개를 이용하면 추력을 증가한다. 가설 3. Cycloidal propeller의 날개에 wing fence 구조를 설치하면 추력 개선 효과가 있다.
다. 작품의 주요 내용
[A - 1] : 파이썬을 이용한 Flap Angle Distribution 찾기
[A - 2] : Cyclodial Propeller 3D 모델링 이후 조립
[A - 3] : Cyclodial Propeller 날개 구조별 추력 테스트
[B - 가설 1 검증] : CFD를 이용한 날개에 가해지는 Drag 비교 실험 [C – 가설 3 검증] : CFD를 이용한 날개로 얻어지는 추력 비교 실험
3. 탐구(연구) 결과
가설 1.
RoundFlap을 이용한 날개의 경우, StraightFlap을 적용한 날개에 비해서 15.77% 성능 증가가 있 었다. 이는 앞서 제시한 유선형 저항 감소의 원인으로 파악된다.
가설 2.
RoundFlap을 이용한 날개의 경우, StraightFlap을 적용한 날개에 비해서 15.77% 성능 증가가 있 었으며, 이는 앞서 제시한 Pitch Angle의 증가로 인한 것으로 예상된다.
가설 3.
실험적으로 StraightFlap 보다 Wing fence를 적용한 Straightflap을 사용하였을 때 54.55%의 성능 증 가가 있었다.

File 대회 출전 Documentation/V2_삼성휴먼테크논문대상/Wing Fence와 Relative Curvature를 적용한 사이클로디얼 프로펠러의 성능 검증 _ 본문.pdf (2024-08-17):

30th Humantech Paper Award


본 논문에 포함된 정보의 전부 또는 일부를 무단으로 제3자에게 공개, 배포, 복사 또는 사용하는 것을 엄격히 금지합니다. 1 본 논문의 모든 저작권은 저자에게 있습니다.

### 1. 서론

### 1.1 What is a Cyclodial Propeller?

Cyclodial Propeller는 Cyclorotor, Cyclodial Rotor, Cyclogiro등 으로 불리며, 회전 축과 추력 벡터가 수직한 유체 추진 장치 이다. 회전축에 횡방향으로 평행한 날개 (Blade with a spanwise axis parallel to the axis of rotation)를 사용하며 이에 대 한 Pitching motion으로 일관된 추력 벡터를 유지한다. 위에서 언급된 Pitching Motion은 다양한 방식으로 구현될

수 있으나 본 연구에서는 가장 간단하고 대중적으로 사용되 는 Flaparm을 활용한 Pitching Motion을 구현하였다. Flaparm을 이용한 Pitching Motion에 대한 설명

Fig. 1 : Flaparm Pitching Mechanism, [6]
다음과 같은 프로펠러에서, 이심축에 연결되어 날개의 각도 를 조절할 수 있도록 양 고정축에서 회전 가능한 Flaparm이 고정 된 길이로 부착되어 있다. 이 Flaparm은 회전하면서 고정된 이심 축에 의해 날개의 Pitching Motion을 만들어내게 된다. 1.1.2 Cyclodial Propeller의 장점 :

Rapid Thrust Vectoring :
기존의 프로펠러, 제트엔진, 로켓 등은 고정된 방향으로 추력을 내보내게 된다. 이러한 특성으로 인해서 추력의 방향 을 제어할 시에는 추진체 전체를 회전시키는 방식으로 추력 을 제어해야 하는데, 이때 질량이 작지 않은 빠르게 회전하 는 회전체의 큰 회전관성과 자이로힘으로 인해 빠른 방향 전 환이 쉽지 않으며 이로 인해 발생하는 반발력 또한 고려해야 해 기동성에 악영향을 준다. Cyclodial Propeller는 Flaparm에 연 결된 Pitcher를 회전함으로써 회전축에 수직한 방향으로 추

력을 제어할 수 있으므로 작은 회전관성이 작용하는 Thrust Vectoring으로 높은 기동성을 확보하였다. High Advance Ratio thrust:

Advance Ratio란 날개의 회전 중심에 대한 날개의 회전 속 도에 대해 기체의 전진 속력 비를 의미한다. 회전체의 종류 에 따라 수식이 다른데, 프로펠러의 경우 =

(1) (J :
Advance Ratio,
: freestream fluid velocity in m/s, n : rotational speed of propeller in rev/s, D : Diameter of propeller in m)로 주어지 고, 헬리콥터와 Cyclodial Propeller의 경우 =

( : Advance
Ratio, : freestream fluid velocity in m/s, k : Rotor rotational speed in rad/s, r : rotor radius in m)로 주어지게 된다. [1] Cyclodial Propeller의 경우 다양한 요인들에 의해 낮은 Rotational Speed 에서 높은 추력을 얻어낼 수 있는데, 이 특징 덕에 대표적인 VTOL (Vertical Take Off and Landing)인 헬리콥터의 단점인 Retreating Blade Stall을 해결 가능하다. 헬리콥터의 날개는 헬리콥터의 진행방향과 동일한 방향

으로 갈 때와 반대의 방향으로 가는 시점이 헬리콥터의 Sagittal plane을 기준으로 나뉘게 된다. 진행방향의 상대 유체 속도로 인해, 헬기 진행 방향과 반대의 방향으로 가는 날개 는 상대적으로 더 느린 Blade 상대 유체 속도를 가지게 된다. 더 느린 속도는 Lift Equation에 의해 더 낮은 추력을 갖게 되

고, 저하된 추력으로 인해 비행사는 추력을 높이기 위해 헬 리콥터 Blade의 AoA (Angle of Attack)을 증가시키게 된다. 하 지만, 일정 AoA 이후에는 Flow Separature로 인해 Stall Angle에 도달하게 되고, AoA를 증가시키면 추력이 급격하게 떨어지 게 된다. 이러한 위험한 상황으로 인해 헬리콥터는 전진 속 도에 제한이 있다. 하지만 로터의 회전속도가 빠르지 않은 Cyclorotor에서는 이러한 문제가 자연적으로 해결되어 더 높 은 전진속도를 가질 수 있다. Symmetric Thrust :

Cyclodial Propeller는 모든 Blade가 Spanwise-Parallel to Rotational Axis하기 때문에 유체에 대한 상대속도가 모두 같 다는 장점이 있다. 일반적인 Propeller의 경우 중심에 대해 r의 함수로 공기와 접하는 속력이 달라 발생하는 Thrust도 다르

# Wing Fence와 Relative Curvature를 적용한 사이클로디얼

# 프로펠러의 성능 검증

본 연구에서는 회전축과 추력 벡터가 수직한 유체 추진 장치인 Cyclodial Propeller에 Wing Fence와Relative Curvature를 적용하였을 때 가 지게 되는 특성들에 대해서 조사하였다. 주로 Swept Wing 항공기에 적용되는 Wing Fence는 Wingtip Vortice를 감소시켜 추력 효율을 향 상시키고 Stall Angle을 증가시키는 효과가 존재한다. 이러한 Wing Fence를 Cyclodial Propeller에 적용하여 그러한 효과들에 대해 검토하 였다. 또한, 중심축을 통해 회전하는 날개가 받게 되는 Drag을 최소화 시키기 위해 날개의 곡률 반지름을 Rotor의 회전반경과 같도록 하는 Relative Curvature 이론을 적용하였다. 시뮬레이션과 실험으로 검토한 결과, Cyclodial Propeller에 Wing Fence를 적용시 Lift , Drag, Thrust to Power Ratio, 소음 감소에서 성능 향상을 보였다. 반면, Relative Curvature를 적용시에는 Drag 와 Lift 가 모두 감소하였으며 추력 효율이 감소하는 결과를 보였으며 Wing Fence와 Relative Curvature 모두 적용시에도 마찬가지로 성능 증가가 없었음을 확인하였다. 결 과적으로 Relative Curvature 없이 Wing Fence 만 적용하는 것이 성능 향상을 보였다.

30th Humantech Paper Award


2 본 논문에 포함된 정보의 전부 또는 일부를 무단으로 제3자에게 공개, 배포, 복사 또는 사용하는 것을 엄격히 금지합니다. 본 논문의 모든 저작권은 저자에게 있습니다.

고 r이 증가할수록 받는 Thrust 또한 커져 날개가 휘는 문제 또한 설계시 고려해야 한다는 단점이 존재했다. Cyclodial Propeller는 이러한 문제점 없이 간단한 Airfoil 설계로 높은 효 율을 얻어낼 수 있다. Delay of Blade Stall :

Cyclodial Propeller에서의 날개는 Pitcher를 통해 떨어진 이 심축을 기준으로 회전하는 Flaparm에 연결되어 회전하면서 Pitching이 되기 때문에 1회전당 2번 Pitching Motion이 일어나 게 되면서 Pendulum Motion과 같이 날개의 Pitching Motion이 표현된다. 이러한 특성으로 인해 날개의 AoA가 급격하게 증가하고

감소하면서 규칙적이나 반복적인 Lift를 발생시켜 Stall을 지 연시킨다. 이 덕에 더 높은 Stall Angle을 가지게 되어 높은 Advance Ratio에 기여한다. Noise :

낮은 Rotational Speed 덕분에 더 적은 소음이 유발된다. 일 반적인 프로펠러의 경우 Propeller Tip의 속도가 음속을 초과 하게 되는 순간 저항이 급격하게 감소하며 소음으로 인한 에 너지 손실이 극심해져 설계에 한계가 존재하지만 Cyclodial Propeller는 애초에 Rotational Speed가 크지 않아 이러한 고려 사항에서 자유롭다. 1.1.3 Cyclodial Propeller의 단점 :

Blade을 지지하는 Spoke가 같이 회전할 수 밖에 없는데 이 러한 Spoke에서 어쩔수 없이 필연적으로 발생하는 Drag이 존 재한다. 또한, Blade들이 원심력을 많이 받게 되는 구조로 크 기와 강성에 비해 엄청나게 낮은 무게를 가져야 한다. [2]

### 1.2 Wing Fence

스웹트 날개(swept-wing) 항공기가 저속으로 비행할 때, 날개의 전방 모서리 각도로 인해 일부 공기 흐름이 횡방향으로, 즉 날개 끝 쪽으로 이동하게 된다. 날개 중앙 부근의 공기 흐름은 전방 모서리 각도뿐만 아니라 날개 뿌리로부터의 횡방향 공기 흐름 에 영향을 받는다. 이로 인해 날개 끝에서는 공기 흐름이 거의 모두 횡방향으로 이동하게 되어, 추력에 기여하는 효과적인 유 체의 양이 크게 감소해 날개의 추력이 감소하게 된다. 이런 문제를 해결하기 위해 'Wing Fence'의 도입이 필요하다.

'Wing Fence'는 공기 흐름이 너무 멀리 이동하거나 속도가 빨라 져 전체 날개가 한번에 기능을 상실하는 것을 방지하는 역할을 한다. Cyclodial Propeller에서 또한, 날개 양 끝단에서 발생하는 횡 방향 모멘텀을 올바르게 제어하고 추진하기 위해서는 Wing fence의 구조가 필요하다. 1.3 Wingtip device

Wingtip device는 Fixed Wing Aircraft에서 Drag을 감소시켜 추력

효율을 증가시키기 위해 도입하는 장치이다. 날개가 위로 향하 는 추력을 만들어낼 때, 날개의 아랫면은 상대적으로 고기압, 윗 면은 저기압으로 유지되게 된다. 이때, 날개가 있는 면에서는 괜 찮지만 날개의 횡방향으로 끝나는 지점에 근접해서는 아랫면의 고기압 유체가 윗면의 저기압 지역으로 이동하면서 회전하게 된다. 이렇게 형성되는 와류를 Wingtip Vortice라고 하며, 다른 항 공기의 안전을 위협하며 항공기의 Drag을 감소시키는 요소이다. Wingtip Device는 날개의 끝단에 이러한 와류 형성을 막는 벽면

또는 장치를 부착하여 Wingtip Vortice를 감소시키는 것이다.[3]

Fig. 2 : Wingtip Vortice, [3]

### 1.4 Relative Curvature Effect

P.G. Milgliore 등(2012)에 따르면, Darrieus turbine blade 의 공기역학적 특성에는 유체 흐름의 곡률이 중요한 영향을 끼친다. Darrieus turbine은 cyclorotor와 마찬가지 로 익형 구조의 날개를 어떤 축 주위로 회전할 수 있도 록 하는 풍력 발전기이다. 이때 각각의 날개는 곡선 운 동을 하게 되는데, 이 때문에 실제보다 캠버(camber)가 큰 (익형의 휘어진 정도가 큰) 효과가 발생한다고 한 다. 이를 virtual camber effect라 한다. 해당 논문에서는 이를 conformal mapping technique를 이용하여 표현한다. 또한 virtual camber effect의 conformal mapping을 나타낸

Fig. 3에서 보이는 바와 같이 받음각(Angle of Attack, AoA)이 증가하는 효과도 있다.[4]

Fig. 3 : Virtual Camber Effect of Rotating Airfoil [4]

본 연구에서는 Wing Fence와 Relative Curvature라는 두 가지 새 로운 개념을 Cycloidal Propeller에 적용하여 그 성능을 개선하고 자 하는 것이 본 연구의 주요 동기이다. 이때, 본 연구에서 적용한 Wing Fence는 Wingtip Device로의 효

과 또한 존재하여 두 가지 목적 모두로 해석하기 위해 Wingtip Device에 대한 내용 또한 첨부하였다. 2. 연구 방법 및 이론


본 논문에 포함된 정보의 전부 또는 일부를 무단으로 제3자에게 공개, 배포, 복사 또는 사용하는 것을 엄격히 금지합니다. 3

### 1. 가설과 가설에 대한 근거

### 1.1 Wing Fence에 관련한 가설 (WF로 축약)

WF-1 WF를 적용하면, Lift Coefficient가 증가하게 된다. Durga Priya.G 등( 발행년도)에 따르면, 일반적인 Glider의 날개

에 Wing Fence를 적용하였을 때, Stalling Angle의 증가와 Lift Coefficient를 30%가량 증가시키는데에 도움을 주었으며, 약간의 Drag Coefficient 증가가 있었지만 전체적으로 Lift to Drag Ratio는 증가했음을 알 수 있다. Cyclodial Propeller와 같이 회전하는 구조 에서도 비슷한 작용을 할 것이라 기대 가능 하다.[5]

WF-2 WF를 적용하면, Wingtip Vortice가 감소하여 Drag이 감소 한다. 우리가 실험에서 적용하게 될 WingFence는 Wingtip Device 로의 작용 또한 할 수 있어, Wingtip Vortice를 감소 시킬 수 있다. 이로 인해 유발되는 Wingtip Vortice Drag이 감소할 것으로 예상

된다. WF-3 WF를 적용하면, 추력이 증가한다. 위의 WF-1와 WF-2가

성립함으로 인해 추력이 증가할 것으로 예상된다. WF-4 WF를 적용하면, 동일 추력 대비 소음이 감소한다. 동일

추력일 때 필요한 Blade Speed하고 Watt가 감소하여 소음이 감소 할 것으로 예상된다. 2.1.2 Relative Curvature 에 대한 가설 (RC로 축약)

RC-1 RC를 적용하면, Drag이 감소한다. Flow Curvature 이론에 의해, Propeller에 대한 유체의 이동경로와 동일한 형태의 프로펠 러를 적용하면 Drag을 감소시킬 수 있다. Cycloidal propeller의 회 전 반경과 같은 곡률 반지름의 날개를 이용할 경우, 날개 주위의 유속이 rectilinear flow의 모양을 따르도록 conformal mapping을 하 면 angle of attack이 0인 상황과 대응되며, drag force가 최소이다. 따라서 날개가 지면과 수직인 방향으로 이동할 때도 virtual

camber effect에 의해 drag가 생성되는 편평한 날개에 비해 곡률 반지름이 날개의 회전 반경과 일치하는 날개가 에너지 관점에 서 더 효율적일 것이다. RC-2 RC를 적용하면, 추력 효율이 증가한다. 추력이 발생하

지 않는 구역에서의 Drag이 감소하여 추력 효율이 증가할 것이 다. 날개 자체가 휘어져 있으면 virtual camber effect 외에도 날개 에 camber가 있는 효과가 있어 날개가 cycloidal propeller의 위, 아 래쪽에 있을 때 받는 양력이 더 클 것이다. RC-3 RC를 적용하면 소음이 감소한다. Drag의 감소로 인해

소음이 감소할 것이다. 2. 파이썬을 이용한 Flap Angle Distribution 찾기

Flap의 각도는 주회전축과 이심축 사이 거리, 날개의 반지름, Flap 고정축간 거리에 의해 결정된다. 하지만 이 관계가 비선형

적이기 때문에, 파이썬을 이용해 각도 분배를 찾았다. 아래는 이를 찾기 위한 좌표평면상 좌표 정의이다.

Fig. 4 : 좌표평면 상 거리에 대한 정의
l : Flap에서 두 고정축 간 거리 (두 축은 회전 가능함). 20mm로 설계되었다. L : 주회전축과 Flap이 고정되는 축 사이 거리. CenterArm과

FlapArm 모두 75mm 길이로 설계되었다. d : Pitch Distance, 주회전축과 이심축 간 거리, 본 설계에서는

이 거리를 Variable Pitcher로 바꾸어가면서 활용한다. 그러나, 날개가 정확히 중심에 연결된 것이 아니기 때문에 여

기서 보여지는 Pitch Angle에는 오차가 포함되어 있다. Flap Rotational Axis에서 접하는 직선을 기준으로 AoA를 정하게 되면, 양 또는 음의 편향을 갖게 AoA 결과가 나오기 때문에 이를 포함

해서 계산해주어야 한다. 아래에서는 실험에서 사용한 Pitch Distance 인 6mm, 8mm,

11mm, 13mm에 대한 결과 분석을 하였다. 0mm에 대한 데이터를 통해 AoA (Angle of Attack)보정을 수행하였다. Fig 5에서 Angle of Spoke는 Flap Rotational Axis와 연결된

Mainframe과 Mainframe 회전시 어떠한 고정된 방향 (회전축과 수 직한 벡터) 사이의 각도이다.


4 본 논문에 포함된 정보의 전부 또는 일부를 무단으로 제3자에게 공개, 배포, 복사 또는 사용하는 것을 엄격히 금지합니다. 본 논문의 모든 저작권은 저자에게 있습니다.

Fig. 5 : AoA Graph by Pitch Distance

Fig. 6 : Max AoA by Pitch Distance

Flaparm으로 인해 일어나는 Pitching Motion은 거의 단조화 운동 의 개형을 따른다고 볼 수 있으며, Pitch Distance가 커짐에 따라 Max AoA 또한 훨씬 커진다는 것을 알 수 있다. 이때, Max AoA의 최소가 6mm Distance에서 17.29 deg 인 것을 확인 할 수 있는데, 이 는 일반적인 Rectilinear Flow 에서는 이미 한참 Stall Angle을 넘은 수치이다. 이는 Cyclodial Propeller의 특징으로 높은 Stall Angle을 가진다는 특성에 의한 것이다. 3. Relative Curvature Code

NACA Airfoil을 Csv로 저장하게 되면, 각 점이 Chord 방향의 x 좌표와 Chord에서 수직한 방향으로 뻗은 위와 아래 점으로 표현 되는 것을 확인할 수 있다. 본 연구에서 사용한 Relative Curvature Mapping Method는 그중에서 가장 간단한 원둘레로 Mapping 하는 것이다. Chord이 원 둘레를 따라 굽었다고 가정하고, 해당 원의 점에서 접선에 수직하게 위 아래만큼 이동하여 점을 직는 방식 이다. 이때, 원 둘레의 반지름은 Mainframe의 반지름인 75mm를 기준으로 하였다. 가장 간단하면서 연구에서 추구하는 대상을 얻을 수 있는 방식이다. 4. CFD Simulation을 통한 RC-1 검증

Cycloidal propeller의 날개 구조에 따라 pitch angle이 0일 때 작용 하는 drag force를 비교하기 위해 Autodesk CFD를 이용한 시뮬레 이션을 진행했다. 실제 실험 조건과 같이 지름 500mm인 영역의 중심을 기준으로 반지름 70mm인 원형 궤도를 따라 StraightFlap 또는 RoundFlap을 700 RPM으로 회전시켰다. 유체는 Air, 날개는

ABS(molded)로 설정했다.

Fig. 7 : Rotating Airfoil CFD 총 100 step 동안 시뮬레이션을 작동시켰으며, 91~100 step에서 날개의 중심을 수직으로 관통하는 평면에서 아래 그림과 같이 날개의 진행방향을 기준으로 앞과 뒤 점의 압력을 측정했다.

Fig. 8 : Straight Airfoil & Curved Airfoil in CFD

### 5. CFD Simulation을 통한 WF-3 검증

Cycloidal propeller의 날개에 부착된 Wing fence 구조의 효과를 이론적으로 확인해보기 위해 Autodesk CFD를 이용한 시뮬레이 션을 진행했다. 10m/s의 rectilinear한 공기 흐름 속에서 StraightFlap 과 StraightWF Flap을 각각 pitch angle이 0도, 15도인 경우에 대해 50 step 이후의 결과를 측정했다. 시뮬레이션 영역은 날개를 중 심에 둔 300mm*200mm*500mm 크기의 직육면체이다. 유체는 Air, 날개는 ABS(molded)로 설정했다.

Fig. 9 : Airfoil Lift Test CFD
50 step 정도에 공기의 흐름이 평형상태에 도달했다고 가정하 고 날개를 관통하며 공기 흐름에 수직한 방향으로 자른 평면상 에서 날개의 바로 위쪽의 직선을 따라 공기의 속력을 측정했다. 또한 이때 날개에 작용하는 x, y, z 방향 힘을 측정했다.

Fig. 10 : Airfoil Lift Test CFD

### 6. WF와 RC를 적용한 Cyclodial Propeller의 성능

검증

### 6.1 Cyclodial Propeller 실험의 설계

### 6.1.1 전체 설계에 대한 참고 :


본 논문에 포함된 정보의 전부 또는 일부를 무단으로 제3자에게 공개, 배포, 복사 또는 사용하는 것을 엄격히 금지합니다. 5

Jude Schauer의 Cyclodial Propeller 연구를 참고하여, 베어링을 이용한 간단한 조립방식을 적용하여 설계하였으며 Mainframe Radius하고 날개의 Chord, Wingspan을 적용했다. Jude Schauer의 Cyclodial Propeller는 3000RPM에서 328g의 Thrust를 만들어 낼 수 있으며 일반적인 프로펠러의 중량비와 맞먹을정도로 경량화에 성공했다. Thrust to Weight Ratio 4.69:1, 일반적인 Cyclorotor의 2배 의 수치를 달성하였으며, 328g의 Thrust를 78W에서 뽑아내어 4g/W이라는 수치를 얻어내었다. [6]

### 6.1.2 Airfoil의 설계

Airfoil은 적절한 두께를 가지며 Camber 되어있지 않은 NACA 0012 Airfoil을 기준으로 테스트하였다. Chord 50mm, Wingspan 150mm로 설계하였다. 출력시에 두께는 1mm로 하여 출력하였 다.위키백과에 따르면, 대부분의 Airfoil의 Aerodynamic Center는

Chordwise 1/4 부근에 위치한다고 한다. Flapar이 마운팅되는 위 치는 Flap Rotational Axis에서 20mm 떨어진 곳에 설계하였다. 즉, 첫째 구멍은 Chord에서 12.5mm 떨어진 곳에 위치하고, 두 번쨰

구멍은 그 이후 20mm 떨어진 Chord 위에 중심이 존재한다. Wing Fence의 경우, Airfoil당 두 개씩, 양 끝단에서 3mm 떨어진 곳에서 부터 1mm 만큼 두꺼운 Wing Fence를 만들었다. Wing Fence는 전 체 Airfoil을 5mm 만큼 간격띄우기 해서 (Airfoil의 표면으로부터 5mm만큼 수직하게 떨어진 점들의 집합)만들었다.

Fig. 11 : Airfoil Designs in Fusion 360, Straight, Curved, WF versions

사용하고 테스트한 날개의 종류는, NACA 0012 Straight, No WF

NACA 0012 Straight, WF
NACA 0012 Curved, No WF
NACA 0012 Curved WF, 이렇게 총 4가지에 대해서 실험하 였다. 이 중심에 Insert하고 M2 나사, 순간접착제를 이용하여 구

조물을 고정하고, 윤활유를 발라 회전할 수 있도록 하였다. 베어링은 682OP 베어링을 사용하였다. 6.1.3 Cyclodial Propeller의 설계

Fig. 12 : Mainframe, Flaparm, Full Assembly
Variable Pitcher의 설계. Pitcher는 Rotor Rotational Axis와 Flaparm Rotational Axis를 연결해주는 장치로, Cyclodial Rotor의 Pitching Characteristic을 결정짓는 중요한 요소이다. 이때, Pitch Distance를 한 번에 쉽게 조절 가능하도록 Variable Pitcher를 설계하게 되었 다.

Fig. 13 : Variable Pitcher의 설계
6.1.4Thrust Stand의 설계와 측정 변인의 측정 도구 Thrust Stand는 카본 파이버 파이프 (4-6mm)와 3D 프린팅으로 만든 결합 부품들로 제작하여 테이블에 절연테이프로 부착하였 다. Load Cell과 Motor Stand, Propeller Mount, Tachometer Sensor Mount의 기능을 전부 다 할 수 있도록, 간단한 실험 장비를 만들 었다.


6 본 논문에 포함된 정보의 전부 또는 일부를 무단으로 제3자에게 공개, 배포, 복사 또는 사용하는 것을 엄격히 금지합니다. 본 논문의 모든 저작권은 저자에게 있습니다.

Fig. 14 : Load Cell & Motor, Tachometer, dB Measure, Watt measure 모터는 MT2213 모터를 사용하였으며, GT2 300T Closed Pulley

를 이용하여 풀리와 연결지었다. 그 이외 측정 도구들은 위에 프 로펠러 실험 시 사용한 도구랑 일치한다. 실험 시 바꾸어가며 실 험한 변수는 Power Value to ESC, Pitch Distance, Airfoil Type을 바꾸 어가며 실험하였으며 이때 측정한 값으로는 RPM, 소음 (dB), Power (W)을 측정하였다.

Fig. 15 : 실험한 Airfoil들을 가지고 조립한 Cyclodial Rotor의
모습. 6.1.5 Propeller Test

실제 프로펠러에 비해서 실질적으로 더 좋은 성능을 낼 수 있는지 대조하기 위해 MT2213 모터에 가장 대중적으로 사용되는 10인치 프로펠러를 사용하여, RPM, 소리 (dB), Power(W), Thrust(g)을 측정하였다. 프로펠러의 모델은 1045 Prop이며 중형 이상의 멀티콥터에 가장 흔하게 사용되는 로 터이다.

RPM은 적외선 장애물 센서와 아두이노의 인터럽트를 이 용하여 측정하였으며, 간이 타코미터로 꽤 정밀하게 측정 가 능했다. 소리의 크기는 LUAZ-320이란 데시벨 측정기를 이용 하여 60cm 거리에서 측정하였다. Power는 시중에서 판매되 는 200A High Precision Watt Meter를 이용하여 측정하였으며, Thrust는 1kg Load Cell과 Hx711을 연결하여 아두이노를 통해

측정하였다. 3. 결과

### 3.1. CFD Simulation을 통한 RC-1 검증과 결과

Fig. 16은 91~100 step 범위에서의 StraightFlap, RoundFlap 앞 뒤 압력 데이터이다. 시간, 공간 간격이 완벽히 연속적이지 않 아 압력 값이 많이 바뀌므로 10개 step에 대한 앞뒤 압력차의 평균을 구했다. 단위는 / 이다. 두 날개에 작용하는 drag force는 이 압력차에 비례한다고 근사할 수 있다. 아래 표 에서 확인할 수 있듯이 StraightFlap보다 RoundFlap에서 압력차 가 더 작다. 즉, pitch angle이 0일 때 RoundFlap이 받는 drag force 가 StraightFlap이 받는 drag force보다 작을 것이라 유추할 수 있 다.

Fig. 16 : Drag Force Analysis from CFD

### 3.2. CFD Simulation을 통한 WF-3 검증

Fig. 17은 날개 방향과 나란하며 날개 면과 가까이 있는 선분 위에서 측정한 날개 방향의 속도 분포에 대한 평균과 표준편차 데이터이다. Model 중 ‘NF’는 wing fence 구조가 없는 것, ‘WF’는 wing fence 구조가 있는 것을 의미한다. ‘Normalized’ 열은 속도 분 포를 정규화한 것인데, 서로 다른 실험 환경에서의 데이터를 비 교하기 위해 속력이 최대인 것을 1로 맞추도록 하여 일정한 비 율로 속도 데이터를 변화시킨 데이터이다.


본 논문에 포함된 정보의 전부 또는 일부를 무단으로 제3자에게 공개, 배포, 복사 또는 사용하는 것을 엄격히 금지합니다. 7

Fig. 17 : Spanwise Airflow on WF Airfoil CFD, 속도 단위 m/s 1에 대해 정규화 이후 상대치

아래는 pitch angle이 0도일 때 wing fence 구조가 있는 모델과 없는 모델에 대해 정규화한 속도 데이터를 각각 그래프로 나타 낸 것이다. Wing fence 구조가 없을 때는 속도가 거의 단조 증가 하나, wing fence 구조가 있을 때는 그 주위에서 속력 분포가 0 주 위로 진동하는 것을 알 수 있다. 그 결과 평균적인 날개 방향의 유체 흐름이 더 적고, 표준편차도 작다. Fig 18에서 또한 y축은 속도에 대한 정규화 데이터(최대치를 1

로 삼아 Scale 감소) 이며

Fig. 18 : Normalized Force of Airfoil from CFD

계산한 양력과 drag을 Fig 19에 나타내었다. Pitch angle이 0도일 때보다 15도일 때 전반적으로 큰 양력이 작용한다. 같은 pitch angle에 대해 pitch angle이 0도일 때는 wing fence 구조가 없을 때 보다 있을 때 양력이 매우 크지만, 15도일 때는 양력이 조금 감소 했다. 한편 drag의 경우 두 경우 모두 wing fence 구조가 있을 때 drag force가 작다.

Fig. 19 : Force Analysis from CFD
. 3.3. 실제 실험 결과

### 3.3.1 Propeller Test 결과 :

프로펠러에 대해서는 Thrust Value 17개에 대하여 904~4496 RPM까지 Thrust (g), Power (W), Noise (dB)를 측정하 였으며, 다음 데이터를 첨부한다. 4496rpm, 39.6W에서 337g의 추력을 만들어냈으며 이때 소

음은 81.5dB였다. 최대 추력을 발생시킬 때 Thrust Per Watt (g/W) Ratio는 8.51이었으며 모든 측정치에서 최대치는 11.54 g/W 였다. Max Thrust per Watt 에서 2213Rpm, 6.5W에 75g의 Thrust를 만들었으며 71.4dB를 기록하였다. 이 데이터는 모터와 프로펠러 제조사에서 제공한 정보와

잘 들어맞아 실험이 잘 진행되었음을 알 수 있다. 3.3.2 Cyclodial Propeller 실험 결과 :

Pitch Distance (6mm, 8mm, 11mm, 13mm), 날개 5가지, Thrust Value 20개씩에 대해 4개의 변량을 측정을 하였기 때문에 데 이터의 수가 총 약 1280개로 너무 많아 분석에 필수적인 특징

들로 가공하여 첨부한다. 어떠한 프로펠러가 성능적으로 좋다고 말하기 위해서는, 추력, 에너지 효율, 소음이 모두 좋아야 한다. 이러한 세 조건

을 만족시키는 프로펠러를 수치적으로 찾기 위해 아래와 같 은 수치들을 제시하고 그를 요약하여 정리하였다. CD : Drag Coefficient. 일반적인 항공기에서는

=

(2) 로 표현된다. 본 연구에서는 오로지 받는 힘 과 각속도만 변하므로, 이에 비례할 것이라고 판단되는 Watt / rpm^2 (3)으로 Drag Coefficient에 대해 분석하였다. CL : Lift Coefficient. 위의 서론에서 언급하였으며 본 연구

에서는 Thrust / rpm^2으로 상호 대조를 수행했다. Max thrust : 최대 추력과 최대 추력일 때의 g/W, CD, dB를

조사한다. Max efficiency : 최대 추력 효율을 가질 때의 추력과 CD, dB

를 조사한다. Max Lift Coefficient : 실험에서 각속도가 변함에 따라 CL의

변화가 무의미하게 작아, 최대치로 기입하였다. 아래에서 언급되는 Thrust의 단위는 모두 gram이며, x축에

Cyclodial Propeller의 Variable Pitcher로 조작한 Pitch Distance를 기준으로 그래프를 그렸다.

Fig. 20 : NACA 0012 Straight

Fig. 21 : NACA 0012 Straight WF

Fig. 22 : NACA 0012 Curved


8 본 논문에 포함된 정보의 전부 또는 일부를 무단으로 제3자에게 공개, 배포, 복사 또는 사용하는 것을 엄격히 금지합니다. 본 논문의 모든 저작권은 저자에게 있습니다.

Fig. 23 : NACA 0012 Curved WF

### 4. 고찰 (Discussion)

WF –1 Lift Coefficient 증가 :

Fig. 24 : Graph of Straight VS Straight WF Lift Coefficient

Fig. 25 : Graph of Curved vs CurvedWF Lift Coefficient

위의 결과에 따르면, Straight Version의 경우 8mm와 11mm의 Pitch Distance에서 각각 161%와 168%의 Lift Coefficient 증가가 있 었음을 확인 할 수 있으며, RC 적용 Curved Version의 경우에는 6mm와 8mm의 Pitch Distance에서 각각 129%와 128%의 Lift Coefficient 증가가 있었음을 확인 가능하다. 비록 전 구간에서 확 실한 효과가 있는 것은 아니지만 대체로 좋은 효과를 보여준다 고 요약할 수 있으며 Straight Version에서는 엄청난 성능 증가를 가져다줌을 볼 수 있다. WF-2 WF를 적용하면, Drag이 감소한다. CD at Max thrust, CD at Max Efficiency

Fig. 26 : Straight 와 Curved Airfoil에 WF 적용 시 Max Thrust Efficiency에서 Drag Coefficient 변화율

Fig. 27 : Straight 와 Curved Airfoil에 WF 적용 시 Max Thrust에서 Drag Coefficient 변화율

Drag Coefficient의 변화는 Wing Fence의 유무하고 별로 관계가 없다는 것을 확인할 수 있다. 이는 선행 연구 (Rectilinear Flow에 서 Glider 날개에 Wing Fence 적용 연구)에서 보인 것이랑 같으며, 약간의 Drag Coefficient 증가가 있다고 한 것이랑 일치한다. 따라

서 Wingtip Vortice 감소로 인한 Drag 감소 효과는 미미하다고 요 약 할 수 있다. WF-3 WF를 적용하면, 추력이 증가한다.


본 논문에 포함된 정보의 전부 또는 일부를 무단으로 제3자에게 공개, 배포, 복사 또는 사용하는 것을 엄격히 금지합니다. 9

Fig. 28 : Straight Airfoil에 Wing Fence 적용 시 Max Thrust, Max Efficiency에서의 Thrust, Max Efficiency의 변화율 그래프

Fig. 29: Curved Airfoil에 Wing Fence 적용 시 Max Thrust, Max Efficiency(g/W)에서의 Thrust, Max Efficiency의 변화율 그래프

특이하게도, Straight Version와 RC를 적용한 두 가지의 차이가 확연하게 드러난다. Straight Version에서는 확실하게 WF-3 가설 이 성립하고, 엄청난 효과를 보여준다. 그러나, Curved Version에 서는 그 효과가 미미하고 상관이 없어 보인다. Wing Fence를 적용하게 되면, Straight Airfoil의 경우 확실하게

최대 추력이 증가하고, 최대 효율에서의 추력이 증가하는 경향 이 있으며, Pitch Distance 최적화 시에는 최대 효율까지 40% 증가 하였다. WF-4 WF를 적용하면, 동일 추력 대비 소음이 감소한다.

Fig. 30 : WF 적용시, Curvature 적용 유무에 따라 동일 추력에서의 DB 변화율
Straight와 Curved Airfoil에 대해, Wing Fence가 있고 없는 모델 중에서 더 적은 최고 추력을 가지는 추력을 기준으로 하여 데시 벨을 대조하였다. 이때, Straight Airfoil의 경우 Pitch Distance가 큰 절반에서는 소음 감소 효과를 가졌고, Pitch Distance가 작은 절반 에서는 반대로 소음이 증가하였다. 반면, Curved Airfoil의 경우 전반적으로 조금 감소하거나 그대로였다. RC-1 RC를 적용하면, Drag이 감소한다.

10 본 논문에 포함된 정보의 전부 또는 일부를 무단으로 제3자에게 공개, 배포, 복사 또는 사용하는 것을 엄격히 금지합니다. 본 논문의 모든 저작권은 저자에게 있습니다.

Fig. 31 : RC 적용시, 최대 추력과 최대 추력 효율에서의 Drag Coefficient 변화

11mm Straight vs Curved를 제외하면 전체적으로 감소한다는 것을 알 수 있다. 따라서 RC-1은 대체로 성립한다고 볼 수 있다. Relative Curvature는 Drag을 감소시키는데 기여한다. RC-2 : RC를 적용하면, 추력 효율이 증가한다. RC 적용시

최대추력효율 증가율 6mm | 8mm | 11mm | 13mm
No Wingfence | 8% | 15% | 1% | -15%
Wingfence | -19% | -7% | -9% | -12%
Fig. 32 : RC 적용 시 Max Efficiency (g/W)의 변화율

Wing Fence가 없을때에, 낮은 Pitch Distance에서는 확연한 최 대 추력효율 증가에 도움이 되지만, 13mm에서는 확연하게 감소 된다. 이는 Relative Curvature 적용시에 위 아래에서 원래 상하 대 칭적이었던 Airfoil Pitch 형상이 Curvature로 인해 달라지게 되면 서 효율이 감소한 것으로 추정된다. Wing Fence 적용시에는 확실하게 최대 추력효율을 감소시킨

다. Drag Coefficient의 감소에도 불구하고 추력 효율이 감소했다 는 것은 Lifting Factor가 크게 감소하게 되었다는 것을 의미한다. 따라서 RC는 Drag 감소에는 도움이 되지만 Lifting Factor까지 감

소시키는 요소라고 결론지을 수 있다. RC-3 RC를 적용하면 소음이 감소한다. 아래 표는, 가장 추력

효율이 높은 순간에 dB을 모은 이후, Curvature를 적용하여 얼만 큼의 dB 변화가 있었는지를 나타내는 표이다. 단위는 dB이다. Pitch
Distance | 6mm | 8mm | 11mm | 13mm
No WF Models | 10.4 | 11.3 | 12.8 | 8.9
WF Models | 1 | 1.2 | 7.6 | 7.7

Fig. 33 : Pitch Distance에 따라, RC를 적용하였을 때 RC 없는 모델에 비한 Decibel 변화량

위 표에 의하면, 추력효율이 높은 순간에 dB은 모두 증가하였 음을 확인할 수 있으며, 심지어 매우 큰 폭으로 증가하였다. 이 에 대한 원인을 분석하는 것이 차후 연구의 목표가 되어 더 정숙 한 Cyclodial Propeller를 개발하는데 도움이 되길 바란다. 5. 결론(Conclusion)

WF-1, Lift Coefficient의 증가 : Straight Version의 경우 8mm와 11mm의 Pitch Distance에서 각각 161%와 168%의 Lift Coefficient 증 가가 있었음을 확인 할 수 있으며, RC 적용 Curved Version의 경 우에는 6mm와 8mm의 Pitch Distance에서 각각 129%와 128%의 Lift Coefficient 증가가 있었다. 전 구간에서 증가하는 결과를 얻 은 것은 아니지만 대체로 성립한다. WF-2, Drag의 감소 : Cyclodial Propeller에 Wing Fence를 부착하

는 것은 Drag Coefficient 감소에 도움이 되지 않으며, 실험 결과에 서는 대체로 무관한 경향을 보였다. WF-3, Lift의 증가 : Straight Airfoil의 경우 확실하게 최대 추력

이 증가하고, 최대 효율에서의 추력이 증가하는 경향이 있으며, Pitch Distance 최적화 시에는 최대 추력 효율까지 40% 증가하였

다. 따라서 Cyclodial Propeller에 Wing Fence를 적용하는 것은 확실 한 추력 상승을 일으키며 추력 효율까지 증가시킬 수 있다. WF-4, 소음 감소 : Wing Fence를 사용하는 것은 동일 추력에서

약간의 소음 감소에 도움이 될 수 있다. RC-1, Drag의 감소 : Relative Curvature를 Cyclodial Propeller에 적

용해 로터 반지름과 같은 반경으로 회전 맵핑시키게 되면 최대 24%까지 Drag Coefficient를 감소시킨다. 따라서, Relative Curvature 의 적용은 대부분의 경우에서 Drag Coefficient를 감소시킬 수 있 다.RC-2, 추력 효율의 증가 : Relative Curvature를 Cyclodial Propeller

에 적용하면, 추력 효율이 증가하지 않는다. RC-3, 소음 감소 : Relative Curvature를 사용하는 것은 동일 추

력에서 소음을 증가시킨다. 프로펠러와의 대조 :

전체적으로 추력 효율과 최대 추력에서 아직 크게 밀리지만, 이는 해당 모터에 최적화된 설계가 아닌 실험을 위한 설계로 인

해 그런 것이다. 소음 면에서는 아무리 시끄러워도 프로펠러의 소음인 81.5dB를 넘지 못하였다. 동일 추력에서의 소음 또한 최 적의 Cyclodial Propeller (Pitch Distance 8~11mm, StraightWF) 유사하 거나 더 낮게 나왔다. 따라서 소음과 기동성 면에서 프로펠러보 다 더 월등한 프로펠러를 만드는데 성공하였다고 판단할 수 있 다. 프로펠러는 직경이 커질수록 추력 효율이 급격하게 상승하 는데, 이는 사용가능한 공기의 면적이 넓어짐으로 인한 것이다. 본 연구에서 비교대상으로 사용한 1045propeller는 직경이 10인

치로, 큰 편에 속하지만 직경이 훨씬 작은 6x3 프로펠러의 경우 최대 추력 효율이 4.7g/W으로 알려져 있다. 따라서, 크기의 제한 으로 인해 추력효율이 급변하는 프로펠러와 대조하여 경쟁력이 있을 것으로 생각된다. 6. 제언

전 Pitch Distance 구간에서 뚜렷한 Lift Coefficient 증가를 보이

본 논문에 포함된 정보의 전부 또는 일부를 무단으로 제3자에게 공개, 배포, 복사 또는 사용하는 것을 엄격히 금지합니다. 11

지 않는 이유는 날개의 Pitch가 계속해서 바뀌기 때문으로 추측 한다. 이러한 내용은 차후 연구를 통해 연구하고 싶다. Cyclodial Propeller의 실제 적용을 위해서는 경량화 방법과 손쉬운 조립 방 식에 대한 다양한 모색이 이루어져야 한다. 본 연구에서도 LW PLA로 출력된 경량 Airfoil을 접목하여 실험을 진행하였으나, Airfoil의 강성이 부족하여 회전하면서 휘어 추력 효율과 추력이

심각하게 감소하는 현상이 관찰되었다. 향후 연구에서는 Carbon Fiber, Foam Board, Light Weight PLA등 다양한 소재와 방식을 접 목하여 Wing Fence가 부착된 경량 설계의 프로펠러와 맞먹을 수 있는 Cyclodial Propeller를 개발하고자 한다. 4. 참고문헌

[1] Wikipedia, Advance Ratio, https://en.wikipedia.org/wiki/Advance_ratio, 2023
[2] Wikipedia, Cyclorotor, https://en.wikipedia.org/wiki/Cyclorotor, 2023
[3]Wikipedia, Wingtip Device https://en.wikipedia.org/wiki/Wingtip_device
[4] P. G. Migliore, W. P. Wolfe and J. B. Fanucci, Flow Curvature Effects on Darrieus Turbine Blade Aerodynamics, Published Online:23 May 2012, pp 49-55
[5] Durga Priya.G, D.V.Balaji, Stall Characteristics Study of Aircraft Wing with
Fence, pp 793-794, International Journal of Engineering Research & Technology (IJERT), 2016
[6]Jude Schauer, The Cyclorotor Is Now a Match For Propellers! , https://youtu.be/wp1xkuKjN_Y?si=8z9UAKtrSKfmtEfG, 2022

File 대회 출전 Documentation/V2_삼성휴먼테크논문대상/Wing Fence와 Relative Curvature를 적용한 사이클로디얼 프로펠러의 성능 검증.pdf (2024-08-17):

30th Humantech Paper Award


본 논문에 포함된 정보의 전부 또는 일부를 무단으로 제3자에게 공개, 배포, 복사 또는 사용하는 것을 엄격히 금지합니다. | 1
본 논문의 모든 저작권은 저자에게 있습니다.
1. 서론 (Abstract)
Cycloidal Propeller는 유체 추진 장치로, 항공 및 수상 차량의 추진, 상승, 조종에 중요한 역할을
수행한다. 본 연구에서는 Wing | Fence와 Relative
Curvature라는 | 두 | 가지 | 아이디어를 | Cyclodial
Propeller에 접목한다. Wing Fence는 주로 Swept-wing 항공기에 장착되며, 날개면상에서 공기의 방향을
제어하여 날개의 안정적 추력 향상에 도움을 준다. 반면, Relative Curvature는 축 상에서 회전하는 날개에

대한 상대 곡률을 계산하는 기법이다. 두 개념을 Cycloidal Propeller에 적용하여 성능을 개선하고자 한다. 본 연구에서는 Cycloidal propeller의 성능 개선과

관련하여 다음 세 가설을 세우고, 이를 증명하기 위한 시뮬레이션과 실험을 진행하였다. 가설 1. Cycloidal propeller의 회전 반경과 같은 곡률

반지름의 날개를 이용하면 Drag를 감소시켜 효율을 높일 수 있다. 가설 2. Cycloidal propeller의 회전 반경과 같은 곡률

반지름의 날개를 이용하면 추력을 증가시킬 수 있다. 가설 3. Cycloidal propeller의 날개에 Wing Fence

구조를 설치하면 추력 개선 효과가 있다. 2. 본문

1. 가설에 대한 정성적인 근거
P. G. Migliore의 ‘Flow Curvature Effects on Darrieus Turbine Blade Aerodynamics’[2]에 따르면, Darrieus turbine blade의 공기역학적 특성에는 유체 흐름의 곡률이 중요한 영향을 끼친다. Darrieus turbine은 Cyclorotor와 유사하게 날개를 축 주위로 회전시키는 풍력발전기이다. 이때 각 날개는 곡선 운동을 하게 되는데, 이 때문에 실제보다 캠버(camber)가 큰 (익형의 휘어진 정도가 큰) 효과가 발생하고, 이를 virtual camber effect라 한다. 해당 논문에서는 이를 conformal mapping technique를 이용하여 표현한다.

또한 virtual camber effect에 의해 받음각(Angle of Attack, AoA)이 증가하는 효과도 있다. 가설 1) Cycloidal propeller의 회전 반경과 같은

곡률 | 반지름의 | 날개를 | 이용할 | 경우, | Relative
Curvature에 의해 angle of attack이 0인 상황과 대응되어 drag force가 최소일 것이다. 가설 2) 날개 자체가 휘어져 있으면 virtual

camber effect 외에도 날개에 camber가 있는 효과가 있어 날개가 cycloidal propeller의 위, 아래쪽에 있을 때 받는 양력이 더 클 것이다. 가설 3) Swept-wing 항공기에 설치되는 wing

fence와 마찬가지로, cycloidal propeller의 날개에 wing fence 유사 구조물을 설치하면 Wing Span 방향으로의 유체 흐름을 제어하여 양력이 커질
것이다.
2. CFD를 이용한 가설 검증.

2.1 CFD를 이용한 가설 1 검증
Cycloidal propeller의 날개 구조에 따라 pitch angle이 0일 때 작용하는 drag force를 비교하기 위해 Autodesk CFD를 이용한 시뮬레이션을 진행했다. 실제 실험 조건과 같이 지름 500mm인 영역의

중심을 기준으로 반지름 70mm인 원형 궤도를 따라
StraightFlap | 또는 | RoundFlap을 | 700 | RPM으로
회전시켰다. 유체는 Air, 날개는 ABS(molded)로 설정했다.

그림 1 : A. StraightFlap 앞뒤 압력 측정점 / B. RoundFlap 앞뒤 압력 측정점

2.2 CFD를 이용한 가설 3 검증
Cycloidal propeller의 날개에 부착된 wing fence 구조의 효과를 이론적으로 확인해보기 위해 Autodesk CFD를 이용한 시뮬레이션을 진행했다. 10m/s의 rectilinear한

# Wing Fence와 Relative Curvature를 적용한

# 사이클로디얼 프로펠러의 성능 검증

본 연구에서는 Cycloidal Propeller의 효율 개선을 위해 Wing Fence 구조와 Virtual Camber 효과를 고려한 날개 형상을 적용하는 방안을 모색하였다. Cycloidal Propeller는 회전축이 유체의 이동 방향에 수직인 유체 추진 장치로, 항공 및 수상 차량의 추진, 상승, 조종에 사용된다. 그러나 기존의 Cycloidal

Propeller는 상대 곡률에 의해 전력 손실이 발생하는 문제가 있었다. 이에 본 연구에서는 공력학적 장치인 Wing Fence의 원리를 도입하여 안정성 및 추력을 향상시키고, Relative Curvature 형상을 최적화하여 전력 손실을 줄이는 방안을 제시하였다. Computational Fluid Mechanics를 이용한 실험 결과, 새로운 구조와 형상이 적용된 Cycloidal Propeller는 기존 대비 효율 개선을 보였으며, 이는 향후 항공 및 수상 차량의 추진 시스템에 대한 새로운 접근 방법을 제공할 것으로 기대된다.

30th Humantech Paper Award


2 | 본 논문에 포함된 정보의 전부 또는 일부를 무단으로 제3자에게 공개, 배포, 복사 또는 사용하는 것을 엄격히 금지합니다. 본 논문의 모든 저작권은 저자에게 있습니다.

공기 흐름 속에서 StraightFlap과 StraightWF Flap을 각각 pitch angle이 0도, 15도인 경우에 대해 50 step 이후의 결과를 측정했다. 시뮬레이션 영역은 날개를
중심에 | 둔 | 300mm*200mm*500mm | 크기의
직육면체이다. 유체는 Air, 날개는 ABS(molded)로 설정했다.
3. 실험을 이용한 검증

3.1 실험 설계

그림 2 : A : StraightFlap. B : StraightWF Flap. C : RoundFlap. D : RoundWF Flap

3.2 실험 구성

전류 등 측정장치를 연결하여 모터에 공급되고 있는 에너지를 측정할 수 있게 세팅했다. RoundFlap, StraightFlap, StraightWF Flap, RoundWFFlap에 대해

각각 8번씩 실험하며 측정 순간의 시간에 따른
에너지 전달률(출력)[W]과 양력[g]을 측정했다.
4. 결론
가설 1. Cycloidal propeller의 회전 반경과 같은 곡률 반지름의 날개를 이용하면 drag를 감소시켜 효율을
높일 수 있다. RoundFlap을 | 이용한 | 날개의 | 경우, | StraightFlap을

적용한 날개에 비해서 15.77% 성능 증가가 있었다. 이는 앞서 제시한 유선형 저항 감소의 원인으로

파악된다. 가설 2. Cycloidal propeller의 회전 반경과 같은 곡률

반지름의 날개를 이용하면 추력을 증가시킬 수 있다. RoundFlap을 | 이용한 | 날개의 | 경우, | StraightFlap을

적용한 날개에 비해서 15.77% 성능 증가가 있었으며, 이는 앞서 제시한 AoA의 증가로 인한 것으로

예상된다. 가설 3. Cycloidal propeller의 날개에 wing fence 구조를

설치하면 추력 개선 효과가 있다. Wing fence 구조가 있을 때와 없을 때 날개에

작용하는 양력, drag force, 날개 표면에서 날개와 나란한 방향으로 흐르는 속력 분포를 시뮬레이션으로 분석한 결과, wing fence 구조가 있을 때 날개와 나란한 방향의 속력 성분의 분포가 0에 더 가까우며 밀집되어 있고, 양력 또한 증가함을 확인했다. 즉
가설 | 3은 | 참이다. | 시뮬레이션뿐만 | 아니라
실험적으로도 | 검증되었다. | StraightFlap에 | 비하여
StraightFlapWF 사용 시 54.55%의 성능 증가가 있었다. 위에서 | 언급된 | 성능은, | 모터에 | 공급되는 | W로
발생하는 | 추력을 | 나눈 | 것을 | 성능효율 | 지표로
사용하였다. 3. 참고문헌
[1] | "NACA | Airfoil." | Wikipedia,
https://en.wikipedia.org/wiki/NACA_airfoil.
[2] P. G. Migliore, W. P. Wolfe and J. B. Fanucci, Flow Curvature Effects on Darrieus Turbine Blade Aerodynamics
[3] Hiromichi Akimoto, Yutaka Hara, Takafumi Kawamura, Takuju Nakamura and Yeon-Seung Lee, A conformal mapping

technique to correlate the rotating flow around a wing section of vertical axis wind turbine and an equivalent linear flow around a static wing

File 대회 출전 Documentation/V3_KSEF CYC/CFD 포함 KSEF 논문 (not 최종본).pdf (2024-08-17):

제21회 KSEF과학프로젝트대회

- 1 -
1. 서론

1.1 What is a Cyclodial Propeller?
Cyclodial Propeller는 Cyclorotor, Cyclodial Rotor, Cyclogiro등으로 불리며, 회전 축과 추력 벡터가 수직 한 유체 추진 장치이다. 회전축에 횡방향으로 평행한 날개 (Blade with a spanwise axis parallel to the axis of rotation)를 사용하며 이에 대한 Pitching motion으 로 일관된 추력 벡터를 유지한다. 이러한 Pitching Motion은 다양한 방식으로 구현될 수 있으나 본 연구 에서는 가장 간단하고 대중적으로 사용되는 Flaparm을 활용한 Pitching Motion을 구현하였다.


Fig. 1 : Flaparm Pitching Mechanism, [6]

Fig 1와 같은 프로펠러에서, 이심축에 연결되어 날개 의 각도를 조절할 수 있도록 양 고정축에서 회전 가능 한 Flaparm이 고정된 길이로 부착되어 있다. 이 Flaparm은 회전하면서 고정된 이심축에 의해 날개의 Pitching Motion을 만들어내게 된다. 1.1.1 Cyclodial Propeller의 장점 :

Rapid Thrust Vectoring : 기존의 프로펠러, 제트엔진, 로켓 등은 고정된 방향

으로 추력을 내보내게 된다. 이러한 특성으로 인해서 추력의 방향을 제어할 시에는 추진체 전체를 회전시키 는 방식으로 추력을 제어해야 하는데, 이때 질량이 작 지 않은 빠르게 회전하는 회전체의 큰 회전관성과 자이 로힘으로 인해 빠른 방향 전환이 쉽지 않으며 이로 인 해 발생하는 반발력 또한 고려해야 해 기동성에 악영향 을 준다. Cyclodial Propeller는 Flaparm에 연결된 Pitcher를 회전함으로써 회전축에 수직한 방향으로 추 력을 제어할 수 있으므로 작은 회전관성이 작용하는 Thrust Vectoring으로 높은 기동성을 확보하였다.

## Wing Fence와 Relative Curvature를 적용한 사이클로디얼 프로펠러의 성능 검증 조용우¹안준혁²

## 1서울과학고등학교, ²서울과학고등학교 Performance Review of Wing Fence and Relative Curvature applied

## Cyclodial Propellers Yongwoo Cho¹

, Junhyuk Ahn²
1Seoul Science High School, Seoul, Korea, 2
Seoul Science High School, Seoul, Korea

요 약 본 연구에서는 회전축과 추력 벡터가 수직한 유체 추진 장치인 사이클로디얼 프로펠러에 실속 펜스와 상대 곡률을 적용하였을 때 가지게 되는 특성들에 대해서 조사하였다. 주로 뒤젖힘 날개 항공기에 적용되는 실속 펜스는 날개 끝의 와류를 감소시켜 추력 효율을 향상시키고 임계 받음각 을 증가시키는 효과가 존재한다. 이러한 실속 펜스를 사이클로디얼 프로펠러에 적용하여 그러한 효과들에 대해 검토하였다. 또한, 중심축을 통해 회전 하는 날개가 받게 되는 항력을 최소화 시키기 위해 날개의 곡률 반지름을 로터의 회전반경과 같도록 하는 상대 곡률 이론을 적용하였다. 시뮬레이션과 실험으로 검토한 결과, 사이클로디얼 프로펠러에 실속 펜스를 적용시 추력, 항력, 추력에 대한 전력 소모량 비, 소음 감소에서 성능 향상을 보였다. 최 대의 성능 향상을 보인 실험 구성의 경우, 실속 펜스 적용 시 최대 양력 계수 68%, 최대 추력 67%나 증가하였음을 알 수 있다. 반면, 상대 곡률을 적 용시에는 항력과 추력이 모두 감소하였으며 추력 효율이 감소하는 결과를 보였으며 실속 펜스와 상대 곡률 모두 적용시에도 마찬가지로 성능 증가가 없었음을 확인하였다. 결과적으로 상대 곡률 없이 실속 펜스만 적용하는 것이 성능 향상을 보였다. Abstract This study investigates the characteristics of a cyclodial propeller, a fluid propulsion device where the

axis of rotation and thrust vector are perpendicular, when applied with wing fences and relative curvature. Wing fences, typically used on swept-wing aircraft, reduce wingtip vortices, thereby enhancing thrust efficiency and increasing the critical angle of attack. These effects were examined when applying wing fences to the cyclodial propeller. Additionally, the concept of relative curvature was applied, setting the blade's curvature radius equal to the rotor's rotational radius, to minimize the drag experienced by the blades rotating around the central axis. The results from simulations and experiments showed that applying wing fences to the cyclodial propeller improved performance in thrust, drag, the ratio of thrust to power consumption, and noise reduction. The most effective experimental configuration with wing fences showed up to a 68% increase in maximum lift coefficient and a 67% increase in maximum thrust. Conversely, applying relative curvature resulted in decreased drag and thrust, reducing thrust efficiency, and no performance increase was observed when both wing fences and relative curvature were applied. Consequently, applying only wing fences without relative curvature showed an improvement in performance.

Key Words : Cyclodial Propeller, Noise, Relative Curvature, Thrust, Wing Fence


- 2 -

High Advance Ratio thrust: Advance Ratio란 날개의 회전 중심에 대한 날개의

회전 속도에 대해 기체의 전진 속력 비를 의미한다. 회 전체의 종류에 따라 수식이 다른데, 프로펠러의 경우
- =
(1) (J : Advance Ratio,

: freestream fluid
velocity in m/s, n : rotational speed of propeller in rev/s, D : Diameter of propeller in m)로 주어지고, 헬 리콥터와 Cyclodial Propeller의 경우 =
| ( | :
Advance Ratio, : freestream fluid velocity in m/s, k : Rotor rotational speed in rad/s, r : rotor radius in m)로 주어지게 된다. [1] Cyclodial Propeller의 경우 다양한 요인들에 의해 낮은 Rotational Speed에서 높 은 추력을 얻어낼 수 있는데, 이 특징 덕에 대표적인 VTOL (Vertical Take Off and Landing)인 헬리콥터의 단점인 Retreating Blade Stall을 해결 가능하다. 헬리콥터의 날개는 헬리콥터의 진행방향과 동일한

방향으로 갈 때와 반대의 방향으로 가는 시점이 헬리콥 터의 Sagittal plane을 기준으로 나뉘게 된다. 진행방향 의 유체 속도로 인해, 헬기 진행 방향과 반대의 방향으 로 가는 날개는 더 느린 Blade 상대 유체 속도를 가지 게 된다. 더 느린 속도는 Lift Equation에 의해 더 낮은 추력을 갖게 되고, 저하된 추력을 상쇄하기 위해 비행 사는 헬리콥터 Blade의 AoA (Angle of Attack)을 증 가시키게 된다. 하지만, 일정 AoA 이후에는 Flow Separature로 인해 Stall Angle에 도달하게 되고, 추력 이 급격하게 떨어지게 된다. 이러한 위험한 상황을 Retreating Blade Stall이라 칭하며, 이로 인해 헬리콥 터는 전진 속도에 제한이 있다. 하지만 로터의 회전속 도가 빠르지 않은 Cyclorotor에서는 이러한 문제가 자 연적으로 해결되어 더 높은 전진속도를 가질 수 있다. Symmetric Thrust : Cyclodial Propeller는 특이적인 구조 덕분에 유체에

대한 상대속도가 모두 같다는 장점이 있다. 일반적인 Propeller의 경우 중심에 대한 거리의 함수로 공기와 접하는 속력이 달라 발생하는 추력도 다르고 그로 인해 날개가 휘는 문제가 있어 설계가 복잡하다는 단점이 있 다. Cyclodial Propeller는 이러한 문제점 없이 간단한 Airfoil 설계로 높은 효율을 얻어낼 수 있다. Delay of Blade Stall : Cyclodial Propeller에서의 날개는 Pitcher를 통해

떨어진 이심축을 기준으로 회전하는 Flaparm에 연결되 어 회전하면서 Pitching이 되기 때문에 1회전당 2번 Pitching Motion이 일어나게 되면서 Pendulum Motion 과 같이 날개의 Pitching Motion이 표현된다. 이러한 특성으로 인해 날개의 AoA가 급격하게 증가

하고 감소하면서 규칙적이나 반복적인 Lift를 발생시켜 Stall을 지연시킨다. 이 덕에 더 높은 Stall Angle을 가 지게 되어 높은 Advance Ratio에 기여한다. Noise : 낮은 회전속도로 인해 더 적은 소음이 발생한다. 일

반적인 프로펠러의 경우 Propeller Tip의 속도가 음속 을 초과하게 되는 순간 저항이 급격하게 증가하여 엄청 난 소음이 발생하지만 Cyclodial Propeller는 작은 회 전속도로 이러한 고려사항에서 자유롭다.

1.1.2 Cyclodial Propeller의 단점 :

Blade을 지지하는 Spoke가 같이 회전할 수 밖에 없 는데 이러한 Spoke에서 어쩔수 없이 필연적으로 발생 하는 Drag이 존재한다. 또한, Blade들이 원심력을 많이 받게 되는 구조로 크기와 강성에 비해 엄청나게 낮은 무게를 가져야 한다. [2]

1.2 Wing Fence :
스웹트 날개(swept-wing) 항공기가 저속으로 비행 할 때, 날개의 전방 모서리 각도로 인해 일부 공기 흐 름이 횡방향으로, 즉 날개 끝 쪽으로 이동하게 된다. 날 개 중앙 부근의 공기 흐름은 전방 모서리 각도뿐만 아 니라 날개 뿌리로부터의 횡방향 공기 흐름에 영향을 받 는다. 이로 인해 날개 끝에서는 공기 흐름이 거의 모두 횡방향으로 이동하게 되어, 추력에 기여하는 효과적인 유체의 양이 크게 감소해 날개의 추력이 감소하게 된다. 이런 문제를 해결하기 위해 'Wing Fence'의 도입이

필요하다. 'Wing Fence'는 공기 흐름이 너무 멀리 이동 하거나 속도가 빨라져 전체 날개가 한번에 기능을 상실 하는 것을 방지하는 역할을 한다. Cyclodial Propeller 에서 또한, 날개 양 끝단에서 발생하는 횡방향 모멘텀 을 올바르게 제어하고 추진하기 위해서는 Wing fence 의 구조가 필요하다. 1.3 Wingtip device

Wingtip device는 Fixed Wing Aircraft에서 Drag을 감소시켜 추력효율을 증가시키기 위해 도입하는 장치이 다. 날개가 위로 향하는 추력을 만들어낼 때, 날개의 아 랫면은 상대적으로 고기압, 윗면은 저기압으로 유지되 게 된다. 이때, 날개가 있는 면에서는 괜찮지만 날개의 횡방향으로 끝나는 지점에 근접해서는 아랫면의 고기압 유체가 윗면의 저기압 지역으로 이동하면서 회전하게 된다. 이렇게 형성되는 와류를 Wingtip Vortice라고 하 며, 다른 항공기의 안전을 위협하며 항공기의 Drag을 감소시키는 요소이다. Wingtip Device는 날개의 끝단에 이러한 와류 형성을 막는 벽면 또는 장치를 부착하여 Wingtip Vortice를 감소시키는 것이다. [3]

Fig. 2 : Wingtip Vortice, [3]
1.4 Relative Curvature Effect

P.G. Milgliore 등(2012)에 따르면, Darrieus turbine blade의 공기역학적 특성에는 유체 흐름의 곡 률이 중요한 영향을 끼친다. Darrieus turbine은 cyclorotor와 마찬가지로 익형 구조의 날개를 어떤 축 주위로 회전할 수 있도록 하는 풍력 발전기이다. 이때 각각의 날개는 곡선 운동을 하게 되는데, 이 때

문에 실제보다 캠버(camber)가 큰 (익형의 휘어진 정도가 큰) 효과가 발생한다고 한다. 이를 virtual
camber | effect라 | 한다. | 해당 | 논문에서는 | 이를

- 3 -

conformal mapping technique를 이용하여 표현한다. 또한 virtual camber effect의 conformal mapping을

나타낸 Fig. 3에서 보이는 바와 같이 받음각(Angle of Attack, AoA)이 증가하는 효과도 있다. [4]


Fig. 3 : Virtual Camber Effect of Rotating Airfoil [4]

본 연구에서는 Wing Fence와 Relative Curvature라 는 두 가지 새로운 개념을 Cycloidal Propeller에 적용 하여 그 성능을 개선하고자 하는 것이 본 연구의 주요 동기이다. 이때, 본 연구에서 적용한 Wing Fence는 Wingtip

Device로의 효과 또한 존재하여 두 가지 목적 모두로 해석하기 위해 Wingtip Device에 대한 내용 또한 첨부

### 하였다. 2. 연구 방법 및 이론

1. 가설과 가설에 대한 근거

1.1 Wing Fence에 관련한 가설 (WF로 축약)

WF-1 WF를 적용하면, Lift Coefficient가 증가하게 된 다. Durga Priya.G 등 (2016)에 따르면, 일반적인 Glider 의 날개에 Wing Fence를 적용하였을 때, Stalling Angle의 증가와 Lift Coefficient를 30%가량 증가시키는데에 도움 을 주었으며, 약간의 Drag Coefficient 증가가 있었지만 전체적으로 Lift to Drag Ratio는 증가했음을 알 수 있다. Cyclodial Propeller와 같이 회전하는 구조에서도 비슷한

작용을 할 것이라 기대 가능 하다. [5]

WF-2 WF를 적용하면, Wingtip Vortice가 감소하여
Drag이 | 감소한다. | 우리가 | 실험에서 | 적용하게 | 될
WingFence는 Wingtip Device 로의 작용 또한 할 수 있 어, Wingtip Vortice를 감소 시킬 수 있다. 이로 인해 유발 되는 Wingtip Vortice Drag이 감소할 것으로 예상된다. WF-3 WF를 적용하면, 추력이 증가한다. 위의 WF-1

와 WF-2가 성립함으로 인해 추력이 증가할 것으로 예상 된다. WF-4 WF를 적용하면, 동일 추력 대비 소음이 감소한

다. 동일 추력일 때 필요한 Blade Speed하고 Watt가 감 소하여 소음이 감소할 것으로 예상된다.

2.1.2 Relative Curvature 에 대한 가설 (RC로 축약)

RC-1 RC를 적용하면, Drag이 감소한다. Flow Curvature 이론에 의해, Propeller에 대한 유체의 이동 경로와 동일한 형태의 프로펠러를 적용하면 Drag을 감 소시킬 수 있다. Cycloidal propeller의 회전 반경과 같 은 곡률 반지름의 날개를 이용할 경우, 날개 주위의 유 속이 rectilinear flow의 모양을 따르도록 conformal mapping을 하면 angle of attack이 0인 상황과 대응되 며, drag force가 최소이다. 따라서 날개가 지면과 수직 인 방향으로 이동할 때도 virtual camber effect에 의해 drag가 생성되는 편평한 날개에 비해 곡률 반지름이 날개의 회전 반경과 일치하는 날개가 에너지 관점에서 더 효율적일 것이다. RC-2 RC를 적용하면, 추력 효율이 증가한다. 추력

이 발생하지 않는 구역에서의 Drag이 감소하여 추력 효율이 증가할 것이다. 날개 자체가 휘어져 있으면 virtual camber effect 외에도 날개에 camber가 있는 효과가 있어 날개가 cycloidal propeller의 위, 아래쪽 에 있을 때 받는 양력이 더 클 것이다. RC-3 RC를 적용하면 소음이 감소한다. Drag의 감소

로 인해 소음이 감소할 것이다. 2. 파이썬을 이용한 Flap Angle Distribution 찾기

Flap의 각도는 주회전축과 이심축 사이 거리, 날개의 반지름, Flap 고정축간 거리에 의해 결정된다. 하지만 이 관계가 비선형적이기 때문에, 파이썬을 이용해 각도 분배를 찾았다. 아래는 이를 찾기 위한 좌표평면상 좌표 정의이다.


Fig. 4 : 좌표평면 상 거리에 대한 정의
l : Flap에서 두 고정축 간 거리 (두 축은 회전 가능 함). 20mm로 설계되었다. L : 주회전축과 Flap이 고정되는 축 사이 거리. CenterArm과 FlapArm 모두 75mm 길이로 설계되었

다.d : Pitch Distance, 주회전축과 이심축 간 거리, 본

설계에서는 이 거리를 Variable Pitcher로 바꾸어가면 서 활용한다. 그러나, 날개가 정확히 중심에 연결된 것이 아니기

때문에 여기서 보여지는 Pitch Angle에는 오차가 포함


- 4 -

되어 있다. Flap Rotational Axis에서 접하는 직선을 기 준으로 AoA를 정하게 되면, 양 또는 음의 편향을 갖게 AoA 결과가 나오기 때문에 이를 포함해서 계산해주어 야 한다. 이를 포함한 AoA는 Airfoil의 Chord 상 중심 에서 회전반경의 접선을 기준 0도로 사용하였다. 아래에서는 실험에서 사용한 Pitch Distance 인

6mm, 8mm, 11mm, 13mm에 대한 결과 분석을 하였다. 0mm에 대한 데이터를 통해 AoA (Angle of Attack)보

정을 수행하였다. Fig 5에서 Angle of Spoke는 Flap Rotational Axis와

연결된 Mainframe과 Mainframe 회전시 어떠한 고정 된 방향 (회전축과 수직한 벡터) 사이의 각도이다.


Fig. 5 : AoA Graph by Pitch Distance


Fig. 6 : Max AoA by Pitch Distance

Flaparm으로 인해 일어나는 Pitching Motion은 거의 단조화 운동의 개형을 따른다고 볼 수 있으며, Pitch Distance가 커짐에 따라 Max AoA 또한 훨씬 커진다 는 것을 알 수 있다. 이때, Max AoA의 최소가 6mm Distance에서 17.29 deg 인 것을 확인 할 수 있는데, 이는 일반적인 Rectilinear Flow 에서는 이미 한참

Stall | Angle을 | 넘은 | 수치이다. | 이는 | Cyclodial
Propeller의 특징으로 높은 Stall Angle을 가진다는 특 성에 의한 것이다. 3. Relative Curvature Code

NACA Airfoil을 Csv로 저장하게 되면, 각 점이 Chord 방향의 x좌표와 Chord에서 수직한 방향으로 뻗 은 위와 아래 점으로 표현되는 것을 확인할 수 있다. 본 연구에서 사용한 Relative Curvature Mapping

Method는 회전반경의 둘레로 Chord를 맵핑하는 것이 다. Chord이 회전반경 둘레를 따라 굽었다고 가정하고, 해당 원의 점에서 접선에 수직하게 위 아래만큼 이동하

여 점을 찍는 방식이다. 가장 간단하면서 연구에서 추 구하는 대상을 얻을 수 있는 방식이다.

4. CFD Simulation을 통한 RC-1 검증

Cycloidal propeller의 날개 구조에 따라 pitch angle 이 0일 때 작용하는 drag force를 비교하기 위해 Autodesk CFD를 이용한 시뮬레이션을 진행했다. 실제 실험 조건과 같이 지름 500mm인 영역의 중심을 기준 으로 반지름 70mm인 원형 궤도를 따라 StraightFlap 또는 RoundFlap을 700 RPM으로 회전시켰다. 유체는 Air, 날개는 ABS(molded)로 설정했다.


Fig. 7 : Rotating Airfoil CFD
총 100 step 동안 시뮬레이션을 작동시켰으며, 91~100 step에서 날개의 중심을 수직으로 관통하는

평면에서 아래 그림과 같이 날개의 진행방향을 기준으 로 앞과 뒤 점의 압력을 측정했다.

Fig. 8 : Straight Airfoil & Curved Airfoil in CFD

5. CFD Simulation을 통한 WF-3 검증

Cycloidal propeller의 날개에 부착된 Wing fence 구 조의 효과를 이론적으로 확인해보기 위해 Autodesk
CFD를 | 이용한 | 시뮬레이션을 | 진행했다. | 10m/s의
rectilinear한 | 공기 | 흐름 | 속에서 | StraightFlap과
StraightWF Flap을 각각 pitch angle이 0도, 15도인 경 우에 대해 50 step 이후의 결과를 측정했다. 시뮬레이 션 영역은 날개를 중심에 둔 300mm*200mm*500mm
크기의 | 직육면체이다. | 유체는 | Air, | 날개는
ABS(molded)로 설정했다.


Fig. 9 : Airfoil Lift Test CFD


- 5 -

50 step 정도에 공기의 흐름이 평형상태에 도달했다고 가정하고 날개를 관통하며 공기 흐름에 수직한 방향으로 자른 평면상에서 날개의 바로 위쪽의 직선을 따라 공기의 속력을 측정했다. 또한 이때 날개에 작용하는 x, y, z 방향 힘을 측정했다.


Fig. 10 : Airfoil Lift Test CFD

6. WF와 RC를 적용한 Cyclodial Propeller의 검증

6.1 Cyclodial Propeller 실험의 설계

6.1.1 전체 설계에 대한 참고 :

Jude Schauer의 Cyclodial Propeller 연구를 참고하여, 베어링을 이용한 간단한 조립방식을 적용하여 설계하였으

며 Mainframe Radius하고 날개의 Chord, Wingspan을 적
용했다. | Jude | Schauer의 | Cyclodial | Propeller는
3000RPM에서 328g의 Thrust를 만들어 낼 수 있으며 일반적인 프로펠러의 중량비와 맞먹을정도로 경량화에 성
공했다. | Thrust to Weight Ratio 4.69:1, 일반적인
Cyclorotor의 | 2배의 | 수치를 | 달성하였으며, | 328g의
Thrust를 78W에서 뽑아내어 4g/W이라는 수치를 얻어내 었다. [6]

6.1.2 Airfoil의 설계

Airfoil은 적절한 두께를 가지며 Camber 되어있지 않은 NACA 0012 Airfoil을 기준으로 테스트하였다. Chord 50mm, Wingspan 150mm로 설계하였다. 출력시

에 두께는 1mm로 하여 출력하였다. 위키백과에 | 따르면, | 대부분의 | Airfoil의

Aerodynamic Center는 Chordwise 1/4 부근에 위치한
다고 | 한다. | Flapar이 | 마운팅되는 | 위치는 | Flap
Rotational Axis에서 20mm 떨어진 곳에 설계하였다. 즉, 첫째 구멍은 Chord에서 12.5mm 떨어진 곳에 위

치하고, 두 번쨰 구멍은 그 이후 20mm 떨어진 Chord 위에 중심이 존재한다. Wing Fence의 경우, Airfoil당 두 개씩, 양 끝단에서 3mm 떨어진 곳에서부터 1mm 만큼 두꺼운 Wing Fence를 만들었다. Wing Fence는 전체 Airfoil을 5mm 만큼 간격띄우기 해서 (Airfoil의 표면으로부터 5mm만큼 수직하게 떨어진 점들의 집합) 만들었다.

Fig. 11 : Airfoil Designs in Fusion 360, Straight, Curved, WF versions

사용하고 테스트한 날개의 종류는, NACA 0012 Straight, No WF // NACA 0012 Straight, WF // NACA 0012 Curved, No WF // NACA 0012 Curved WF, 이 렇게 총 4가지에 대해서 실험하였다. 이 중심에 Insert하고 M2 나사, 순간접착제를 이용

하여 구조물을 고정하고, 윤활유를 발라 회전할 수 있 도록 하였고, 베어링은 682OP 베어링을 사용하였다. 6.1.3 Cyclodial Propeller의 설계


Fig. 12 : Mainframe, Flaparm, Full Assembly

Variable | Pitcher의 | 설계. | Pitcher는 | Rotor
Rotational Axis와 Flaparm Rotational Axis를 연결해
주는 | 장치로, | Cyclodial | Rotor의 | Pitching
Characteristic을 결정짓는 중요한 요소이다. 이때, Pitch Distance를 한 번에 쉽게 조절 가능하도록

Variable Pitcher를 설계하게 되었다.


- 6 -


Fig. 13 : Variable Pitcher의 설계
6.1.4 Thrust Stand의 설계와 측정 변인의 측정 도구

Thrust Stand는 카본 파이버 파이프 (4-6mm)와 3D 프린팅으로 만든 결합 부품들로 제작하여 테이블에 절연
테이프로 | 부착하였다. | Load | Cell과 | Motor | Stand,
Propeller Mount, Tachometer Sensor Mount의 기능을 전부 다 할 수 있도록, 간단한 실험 장비를 만들었다.


Fig. 14 : Load Cell & Motor, Tachometer, dB Measure, Watt measure

모터는 MT2213 모터를 사용하였으며, GT2 300T Closed Pulley를 이용하여 풀리와 연결지었다. 그 이외 측 정 도구들은 위에 프로펠러 실험 시 사용한 도구랑 일치 한다. 실험 시 바꾸어가며 실험한 변수는 Power Value to ESC, Pitch Distance, Airfoil Type을 바꾸어가며 실험하 였으며 이때 측정한 값으로는 RPM, 소음 (dB), Power (W)을 측정하였다.


Fig. 15 : 실험한 Airfoil들을 가지고 조립한 Cyclodial Rotor의 모습.

6.1.5 Propeller Test

실제 프로펠러에 비해서 실질적으로 더 좋은 성능을 낼 수 있는지 대조하기 위해 MT2213 모터에 가장 대중적으 로 사용되는 10인치 프로펠러를 사용하여, RPM, 소리 (dB), Power(W), Thrust(g)을 측정하였다. 프로펠러의 모델은 1045 Prop이며 중형 이상의 멀티콥터에 가장 흔 하게 사용되는 로터이다.


Fig. 16 : Propeller Thrust Stand의 모습. Load cell, Motor, IR Sensor, Propeller와 이들의 지지대로 구성되어있다. RPM은 적외선 장애물 센서와 아두이노의 인터럽트

를 이용하여 측정하였으며, 간이 타코미터로 꽤 정밀하 게 측정 가능했다. 소리의 크기는 LUAZ-320이란 데 시벨 측정기를 이용하여 60cm 거리에서 측정하였다. Power는 시중에서 판매되는 200A High Precision

Watt Meter를 이용하여 측정하였으며, Thrust는 1kg Load Cell과 Hx711을 연결하여 아두이노를 통해 측정
하였다. | 3. 결과
3.1. CFD Simulation을 통한 RC-1 검증과 결과 Fig. 17은 91~100 step 범위에서의 StraightFlap, RoundFlap 앞뒤 압력 데이터이다. 시간, 공간 간격이 완벽히 연속적이지 않아 압력 값이 많이 바뀌므로 10 개 step에 대한 앞뒤 압력차의 평균을 구했다. 단위는 / 이다. 두 날개에 작용하는 drag force는 이 압력차에 비례한다고 근사할 수 있다. 아래 표에서 확 인할 수 있듯이 StraightFlap보다 RoundFlap에서 압력 차가 더 작다. 즉, pitch angle이 0일 때 RoundFlap이 받는 drag force가 StraightFlap이 받는 drag force보 다 작을 것이라 유추할 수 있다.

Fig. 17 : Drag Force Analysis from CFD


- 7 -
3.2. CFD Simulation을 통한 WF-3 검증

Fig. 18은 날개 방향과 나란하며 날개 면과 가까이 있는 선분 위에서 측정한 날개 방향의 속도 분포에 대 한 평균과 표준편차 데이터이다. Model 중 ‘NF’는 wing fence 구조가 없는 것, ‘WF’는 wing fence 구조 가 있는 것을 의미한다. ‘Normalized’ 열은 속도 분포 를 정규화한 것인데, 서로 다른 실험 환경에서의 데이 터를 비교하기 위해 속력이 최대인 것을 1로 맞추도록 하여 일정한 비율로 속도 데이터를 변화시킨 데이터이 다.

Fig. 18 : Spanwise Airflow on WF Airfoil CFD, 속도 단위 m/s 1에 대해 정규화 이후 상대치

아래는 pitch angle이 0도일 때 wing fence 구조가 있는 모델과 없는 모델에 대해 정규화한 속도 데이터를 각각 그래프로 나타낸 것이다. Wing fence 구조가 없을 때는 속도가 거의 단조 증가하나, wing fence 구조가 있을 때는 그 주위에서 속력 분포가 0 주위로 진동하 는 것을 알 수 있다. 그 결과 평균적인 날개 방향의 유 체 흐름이 더 적고, 표준편차도 작다. Fig 19에서 또한 y축은 속도에 대한 정규화 데이터

(최대치를 1로 삼아 Scale 감소) 이며

Fig. 19 : Normalized Force of Airfoil from CFD

계산한 양력과 drag을 Fig 19에 나타내었다. Pitch angle이 0도일 때보다 15도일 때 전반적으로 큰 양력 이 작용한다. 같은 pitch angle에 대해 pitch angle이 0 도일 때는 wing fence 구조가 없을 때보다 있을 때 양 력이 매우 크지만, 15도일 때는 양력이 조금 감소했다. 한편 drag의 경우 두 경우 모두 wing fence 구조가 있

을 때 drag force가 작다.


Fig. 20 : Force Analysis from CFD
. 3.3. 실제 실험 결과

3.3.1 Propeller Test 결과 :

프로펠러에 대해서는 Thrust Value 17개에 대하여 904~4496 RPM까지 Thrust (g), Power (W), Noise (dB)를 측정하였으며, 다음 데이터를 첨부한다. 4496rpm, 39.6W에서 337g의 추력을 만들어냈으며

이때 소음은 81.5dB였다. 최대 추력을 발생시킬 때 Thrust Per Watt (g/W) Ratio는 8.51이었으며 모든 측 정치에서 최대치는 11.54 g/W 였다. Max Thrust per Watt 에서 2213Rpm, 6.5W에 75g의 Thrust를 만들 었으며 71.4dB를 기록하였다. 이 데이터는 모터와 프로펠러 제조사에서 제공한 정

보와 잘 들어맞아 실험이 잘 진행되었음을 알 수 있다. 3.3.2 Cyclodial Propeller 실험 결과 :

Pitch Distance (6mm, 8mm, 11mm, 13mm), 날개 5가지, Thrust Value 20개씩에 대해 4개의 변량을 측 정을 하였기 때문에 데이터의 수가 총 약 1280개로 너 무 많아 분석에 필수적인 특징들로 가공하여 첨부한다. 어떠한 프로펠러가 성능적으로 좋다고 말하기 위해

서는, 추력, 에너지 효율, 소음이 모두 좋아야 한다. 이 러한 세 조건을 만족시키는 프로펠러를 수치적으로 찾 기 위해 아래와 같은 수치들을 제시하고 그를 요약하여 정리하였다. CD : Drag Coefficient. 일반적인 항공기에서는

=

(2) 로 표현된다. 본 연구에서는 오로지

받는 힘과 각속도만 변하므로, 이에 비례할 것이라고 판단되는 Watt / rpm^2 (3)으로 Drag Coefficient에 대해 분석하였다. CL : Lift Coefficient. 위의 서론에서 언급하였으며 본

연구에서는 Thrust / rpm^2으로 상호 대조를 수행했 다. Max thrust : 최대 추력과 최대 추력일 때의 g/W, CD,

dB를 조사한다. Max efficiency : 최대 추력 효율을 가질 때의 추력과

CD, dB를 조사한다. Max Lift Coefficient : 실험에서 각속도가 변함에 따

라 CL의 변화가 무의미하게 작아, 최대치로 기입하였 다. 아래에서 언급되는 Thrust의 단위는 모두 gram이며, x축에 Cyclodial Propeller의 Variable Pitcher로 조작

한 Pitch Distance를 기준으로 그래프를 그렸다.

Fig. 21 : NACA 0012 Straight

Fig. 22 : NACA 0012 Straight WF


- 8 -

Fig. 23 : NACA 0012 Curved

Fig. 24 : NACA 0012 Curved WF

### 4. 고찰 (Discussion)

WF –1 Lift Coefficient 증가 :

Fig. 25 : Straight Airfoil에 WF를 적용하였을 때, Max Lift Coefficient의 증가율

Fig. 26 : Graph of Curved vs CurvedWF Lift Coefficient

위의 결과에 따르면, Straight Version의 경우 8mm 와 11mm의 Pitch Distance에서 각각 161%와 168% 의 Lift Coefficient 증가가 있었음을 확인 할 수 있으 며, RC 적용 Curved Version의 경우에는 6mm와 8mm의 Pitch Distance에서 각각 129%와 128%의 Lift Coefficient 증가가 있었음을 확인 가능하다. 비록 전 구간에서 확실한 효과가 있는 것은 아니지만 대체로 좋은 효과를 보여준다고 요약할 수 있으며 Straight Version에서는 엄청난 성능 증가를 가져다줌을 볼 수 있다.

WF-2 WF를 적용하면, Drag이 감소한다. CD at Max thrust, CD at Max Efficiency

Fig. 27 : Straight 와 Curved Airfoil에 WF 적용 시 Max Thrust 에서 Drag Coefficient 변화율

Fig. 28 : Straight 와 Curved Airfoil에 WF 적용 시 Max Thrust Efficiency에서 Drag Coefficient 변화율

Drag Coefficient의 변화는 Wing Fence의 유무하고 별로 관계가 없다는 것을 확인할 수 있다. 이는 선행 연구 (Rectilinear Flow에서 Glider 날개에 Wing Fence 적용 연구)에서 보인 것이랑 같으며, 약간의 Drag Coefficient 증가가 있다고 한 것이랑 일치한다. 따라서 Wingtip Vortice 감소로 인한 Drag 감소 효과

는 미미하다고 요약 할 수 있다. WF-3 WF를 적용하면, 추력이 증가한다.

Fig. 29 : Straight Airfoil에 Wing Fence 적용 시, Max Thrust, Thrust at Max Efficiency, Max Efficiency의 변화율


- 9 -

Fig. 30 : Curved Airfoil에 Wing Fence 적용 시, Max Thrust, Thrust at Max Efficiency, Max Efficiency의 변화율

특이하게도, | Straight | Version와 | RC를 | 적용한
Curved Airfoil 두 가지의 차이가 확연하게 드러난다. Straight Version에서는 확실하게 WF-3 가설이 성립
하고, | 엄청난 | 효과를 | 보여준다. | 그러나, | Curved
Version에서는 그 효과가 미미하고 상관이 없어 보인 다.Wing Fence를 적용하게 되면, Straight Airfoil의 경

우 확실하게 최대 추력이 증가하고, 최대 효율에서의 추력이 증가하는 경향이 있으며, Pitch Distance 최적화 시에는 최대 효율까지 40% 증가하였다. WF-4 WF를 적용하면, 동일 추력 대비 소음이 감소한다.

Fig. 35 : WF 적용시, Curvature 적용 유무에 따라 동일 추 력에서의 DB 변화율
Straight와 Curved Airfoil에 대해, Wing Fence가 있고 없는 모델 중에서 더 적은 최고 추력을 가지는 추
력을 | 기준으로 | 하여 | 데시벨을 | 대조하였다. | 이때, Straight Airfoil의 경우 Pitch Distance가 큰 절반에서

는 소음 감소 효과를 가졌고, Pitch Distance가 작은 절 반에서는 반대로 소음이 증가하였다. 반면, Curved Airfoil의 경우 전반적으로 조금 감소하거나 그대로였다. RC-1 RC를 적용하면, Drag이 감소한다.

Fig. 36 : Relative Curvature 적용 시 Max Thrust 에서의 CD 변화

Fig. 37 : RC 적용 시 Max Efficiency에서 CD 변화

11mm Straight vs Curved를 제외하면 전체적으로 감소한다는 것을 알 수 있다. 따라서 RC-1은 대체로 성립한다고 볼 수 있다. Relative Curvature는 Drag을 감소시키는데 기여한다. RC-2 : RC를 적용하면, 추력 효율이 증가한다.

Fig. 31 : RC 적용 시 Max Efficiency (g/W)의 변화율

Wing Fence가 없을때에, 낮은 Pitch Distance에서는 확연한 최대 추력효율 증가에 도움이 되지만, 13mm에 서는 확연하게 감소된다. 이는 Relative Curvature 적 용시에 위 아래에서 원래 상하 대칭적이었던 Airfoil Pitch 형상이 Curvature로 인해 달라지게 되면서 효율 이 감소한 것으로 추정된다. Wing Fence 적용시에는 확실하게 최대 추력효율을

감소시킨다. Drag Coefficient의 감소에도 불구하고 추 력 효율이 감소했다는 것은 Lifting Factor가 크게 감소 하게 되었다는 것을 의미한다. 따라서 RC는 Drag 감소 에는 도움이 되지만 Lifting Factor까지 감소시키는 요 소라고 결론지을 수 있다. RC-3 RC를 적용하면 소음이 감소한다. 아래 표는, 가장 추력효율이 높은 순간에 dB을 모은

이후, Curvature를 적용하여 얼만큼의 dB 변화가 있었 는지를 나타내는 표이다. 단위는 dB이다.

Fig. 39 : Pitch Distance에 따라, RC를 적용하였을 때 RC 없는 모델에 비한 Decibel 변화량

위 표에 의하면, 추력효율이 높은 순간에 dB은 모두 증가하였음을 확인할 수 있으며, 심지어 매우 큰 폭으 로 증가하였다. 이는 감소한 CL로 인해 동일한 추력을 내기 위해 더 빠른 회전수가 요구되었기 때문으로 해석 된다.

Pitch Distance | Thrust Value | No WF | WF | DB Change
Straight | 6mm | 25g | 66.5dB | 74.5dB | 8.0dB
| 8mm | 48g | 69.6dB | 74.4dB | 4.8dB
| 11mm | 60g | 77.7dB | 71.2dB | -6.5dB
| 13mm | 62g | 77.9dB | 76.0dB | -1.9dB
Curved | 6mm | 26g | 75.8dB | 76.1dB | 0.3dB
| 8mm | 60g | 76.4dB | 74.0dB | -2.4dB
| 11mm | 81g | 78.3dB | 76.0dB | -2.3dB
| 13mm | 84g | 79.0dB | 79.0dB | 0.0dB
RC 적용시 Thrust Efficiency 증가율 | 6mm | 8mm | 11mm | 13mm
No WF | -19% 8% | 15% -7% | -9% 1% | -15% WF -12%
Pitch Distance | 6mm | 8mm | 11mm | 13mm
No WF | 10.4dB | 11.3dB | 12.8dB | 8.9dB
WF | 1.0dB | 1.2dB | 7.6dB | 7.7dB

- 10 -
5. 결론(CONCLUSION)

WF-1, Lift Coefficient의 증가 : Straight Version의 경우 8mm와 11mm의 Pitch Distance에서 각각 161% 와 168%의 Lift Coefficient 증가가 있었음을 확인 할 수 있으며, RC 적용 Curved Version의 경우에는 6mm 와 8mm의 Pitch Distance에서 각각 129%와 128%의 Lift Coefficient 증가가 있었다. 전 구간에서 증가하는 결과를 얻은 것은 아니지만 대체로 성립한다. WF-2, Drag의 감소 : Cyclodial Propeller에 Wing

Fence를 부착하는 것은 Drag Coefficient 감소에 도움 이 되지 않으며, 실험 결과에서는 대체로 무관한 경향 을 보였다. WF-3, Lift의 증가 : Straight Airfoil의 경우 확실하

게 최대 추력이 증가하고, 최대 효율에서의 추력이 증 가하는 경향이 있으며, Pitch Distance 최적화 시에는
최대 | 추력 | 효율까지 | 40% | 증가하였다. | 따라서
Cyclodial Propeller에 Wing Fence를 적용하는 것은 확실한 추력 상승을 일으키며 추력 효율까지 증가시킬 수 있다. WF-4, 소음 감소 : Wing Fence를 사용하는 것은 동
일 추력에서 약간의 소음 감소에 도움이 될 수 있다. RC-1, | Drag의 | 감소 | : | Relative | Curvature를

Cyclodial Propeller에 적용해 로터 반지름과 같은 반 경으로 회전 맵핑시키게 되면 최대 24%까지 Drag Coefficient를 감소시킨다. 따라서, Relative Curvature 의 적용은 대부분의 경우에서 Drag Coefficient를 감소 시킬 수 있다. RC-2, 추력 효율의 증가 : Relative Curvature를

Cyclodial Propeller에 적용하면, 추력 효율이 증가하지 않는다. RC-3, 소음 감소 : Relative Curvature를 사용하는

것은 동일 추력에서 소음을 증가시킨다. 프로펠러와의 대조 : 전체적으로 추력 효율과 최대 추력에서 아직 크게

밀리지만, 이는 해당 모터에 최적화된 설계가 아닌 실 험을 위한 설계로 인해 그런 것이다. 소음 면에서는 아 무리 시끄러워도 프로펠러의 소음인 81.5dB를 넘지 못 하였다. 동일 추력에서의 소음 또한 최적의 Cyclodial Propeller (Pitch Distance 8~11mm, StraightWF) 유 사하거나 더 낮게 나왔다. 따라서 소음과 기동성 면에 서 프로펠러보다 더 월등한 프로펠러를 만드는데 성공 하였다고 판단할 수 있다. 프로펠러는 직경이 커질수록 추력 효율이 급격하게 상승하는데, 이는 사용가능한 공 기의 면적이 넓어짐으로 인한 것이다. 본 연구에서 비 교대상으로 사용한 1045 propeller는 직경이 10인치로, 큰 편에 속하지만 직경이 훨씬 작은 6x3 프로펠러의

경우 최대 추력 효율이 4.7g/W으로 알려져 있다. 따라 서, 크기의 제한으로 인해 추력효율이 급변하는 프로펠 러와 대조하여 경쟁력이 있을 것으로 생각된다.

6. 제언

전 Pitch Distance 구간에서 뚜렷한 Lift Coefficient 증가 를 보이지 않는 이유는 날개의 Pitch가 계속해서 바뀌기 때문으로 추측한다. 이러한 내용은 차후 연구를 통해 연구하고 싶다. Cyclodial Propeller의 실제 적용을 위해서 는 경량화 방법과 손쉬운 조립 방식에 대한 다양한 모 색이 이루어져야 한다. 본 연구에서도 LW PLA로 출력 된 경량 Airfoil을 접목하여 실험을 진행하였으나, Airfoil 의 강성이 부족하여 회전하면서 휘어 추력 효율과 추력 이 심각하게 감소하는 현상이 관찰되었다. 향후 연구에 서는 Carbon Fiber, Foam Board, Light Weight PLA등 다양한 소재와 방식을 접목하여 Wing Fence가 부착된 경량 설 계의 프로펠러와 맞먹을 수 있는 Cyclodial Propeller를

### 개발하고자 한다. References

[1] Wikipedia, Advance Ratio, https://en.wikipedia.org/wiki/Advance_ratio, 2023, (Accessed Sep.,10, 2023)
[2] Wikipedia, Cyclorotor, https://en.wikipedia.org/wiki/Cyclorotor, 2023, (Accessed Sep.,10, 2023)
[3] Wikipedia, Wingtip Device https://en.wikipedia.org/wiki/Wingtip_device, 2023, (Accessed Sep.,10, 2023)
[4] P. G. Migliore, W. P. Wolfe and J. B. Fanucci, Flow Curvature Effects on Darrieus Turbine Blade Aerodynamics, Published Online:23 May 2012, pp 49-55
[5] Durga Priya.G, D.V.Balaji, Stall Characteristics Study of Aircraft Wing with Fence, pp 793-794, International Journal of Engineering Research & Technology (IJERT), 2016
[6] Jude Schauer, The Cyclorotor Is Now a Match For Propellers! , https://youtu.be/wp1xkuKjN_Y?si=8z9UAKtrSKfmtEfG, 2022 (Accessed Sep.,10, 2023)

조용우(Yongwoo Cho)

2022년 2월 : 서일중학교 졸업
2022년 3월~현재 : 서울과학고등
학교 재학
2023년 7월 : 서울과학고등학교 과
제연구 물리과 최우수상
2023년 8월 : 한화사이언스챌린지
2023 대상 수상
2023년 9월 : 김천시 전국무한상상
탐구토론대회 최우수상
2023년 10월 : 서울과학전람회 예선
최우수상
<관심분야>
기계공학, 로봇공학, 컴퓨터공학

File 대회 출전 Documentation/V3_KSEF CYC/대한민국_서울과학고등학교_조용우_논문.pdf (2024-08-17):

제21회 KSEF과학프로젝트대회

- 1 -
1. 서론 1.1 What is a Cyclodial Propeller? Cyclodial Propeller는 Cyclorotor, Cyclodial Rotor,

Cyclogiro등으로 불리며, 회전 축과 추력 벡터가 수직 한 유체 추진 장치이다. 회전축에 횡방향으로 평행한 날개 (Blade with a spanwise axis parallel to the axis of rotation)를 사용하며 이에 대한 Pitching motion으 로 일관된 추력 벡터를 유지한다. 이러한 Pitching Motion은 다양한 방식으로 구현될 수 있으나 본 연구 에서는 가장 간단하고 대중적으로 사용되는 Flaparm을 활용한 Pitching Motion을 구현하였다.


Fig. 1 : Flaparm Pitching Mechanism, [6]

Fig 1와 같은 프로펠러에서, 이심축에 연결되어 날개 의 각도를 조절할 수 있도록 양 고정축에서 회전 가능 한 Flaparm이 고정된 길이로 부착되어 있다. 이 Flaparm은 회전하면서 고정된 이심축에 의해 날개의 Pitching Motion을 만들어내게 된다. 1.1.1 Cyclodial Propeller의 장점 : Rapid Thrust Vectoring : 기존의 프로펠러, 제트엔진, 로켓 등은 고정된 방향

으로 추력을 내보내게 된다. 이러한 특성으로 인해서 추력의 방향을 제어할 시에는 추진체 전체를 회전시키 는 방식으로 추력을 제어해야 하는데, 이때 질량이 작 지 않은 빠르게 회전하는 회전체의 큰 회전관성과 자이 로힘으로 인해 빠른 방향 전환이 쉽지 않으며 이로 인 해 발생하는 반발력 또한 고려해야 해 기동성에 악영향 을 준다. Cyclodial Propeller는 Flaparm에 연결된 Pitcher를 회전함으로써 회전축에 수직한 방향으로 추 력을 제어할 수 있으므로 작은 회전관성이 작용하는 Thrust Vectoring으로 높은 기동성을 확보하였다.

## Wing Fence와 Relative Curvature를 적용한 사이클로디얼 프로펠러의 성능 검증 조용우¹안준혁²

## 1서울과학고등학교, ²서울과학고등학교 Performance Review of Wing Fence and Relative Curvature applied

## Cyclodial Propellers Yongwoo Cho¹

, Junhyuk Ahn²
1Seoul Science High School, Seoul, Korea, 2
Seoul Science High School, Seoul, Korea

요 약 본 연구에서는 회전축과 추력 벡터가 수직한 유체 추진 장치인 사이클로디얼 프로펠러에 실속 펜스와 상대 곡률을 적용하였을 때 가지게 되는 특성들에 대해서 조사하였다. 주로 뒤젖힘 날개 항공기에 적용되는 실속 펜스는 날개 끝의 와류를 감소시켜 추력 효율을 향상시키고 임계 받음각 을 증가시키는 효과가 존재한다. 이러한 실속 펜스를 사이클로디얼 프로펠러에 적용하여 그러한 효과들에 대해 검토하였다. 또한, 중심축을 통해 회전 하는 날개가 받게 되는 항력을 최소화 시키기 위해 날개의 곡률 반지름을 로터의 회전반경과 같도록 하는 상대 곡률 이론을 적용하였다. 시뮬레이션과 실험으로 검토한 결과, 사이클로디얼 프로펠러에 실속 펜스를 적용시 추력, 항력, 추력에 대한 전력 소모량 비, 소음 감소에서 성능 향상을 보였다. 최 대의 성능 향상을 보인 실험 구성의 경우, 실속 펜스 적용 시 최대 양력 계수 68%, 최대 추력 67%나 증가하였음을 알 수 있다. 반면, 상대 곡률을 적 용시에는 항력과 추력이 모두 감소하였으며 추력 효율이 감소하는 결과를 보였으며 실속 펜스와 상대 곡률 모두 적용시에도 마찬가지로 성능 증가가 없었음을 확인하였다. 결과적으로 상대 곡률 없이 실속 펜스만 적용하는 것이 성능 향상을 보였다. Abstract This study investigates the characteristics of a cyclodial propeller, a fluid propulsion device where the

axis of rotation and thrust vector are perpendicular, when applied with wing fences and relative curvature. Wing fences, typically used on swept-wing aircraft, reduce wingtip vortices, thereby enhancing thrust efficiency and increasing the critical angle of attack. These effects were examined when applying wing fences to the cyclodial propeller. Additionally, the concept of relative curvature was applied, setting the blade's curvature radius equal to the rotor's rotational radius, to minimize the drag experienced by the blades rotating around the central axis. The results from simulations and experiments showed that applying wing fences to the cyclodial propeller improved performance in thrust, drag, the ratio of thrust to power consumption, and noise reduction. The most effective experimental configuration with wing fences showed up to a 68% increase in maximum lift coefficient and a 67% increase in maximum thrust. Conversely, applying relative curvature resulted in decreased drag and thrust, reducing thrust efficiency, and no performance increase was observed when both wing fences and relative curvature were applied. Consequently, applying only wing fences without relative curvature showed an improvement in performance.

Key Words : Cyclodial Propeller, Noise, Relative Curvature, Thrust, Wing Fence


- 2 -

High Advance Ratio thrust: Advance Ratio란 날개의 회전 중심에 대한 날개의

회전 속도에 대해 기체의 전진 속력 비를 의미한다. 회 전체의 종류에 따라 수식이 다른데, 프로펠러의 경우
- =
(1) (J : Advance Ratio,

: freestream fluid
velocity in m/s, n : rotational speed of propeller in rev/s, D : Diameter of propeller in m)로 주어지고, 헬 리콥터와 Cyclodial Propeller의 경우 =
| ( | :
Advance Ratio, : freestream fluid velocity in m/s, k : Rotor rotational speed in rad/s, r : rotor radius in m)로 주어지게 된다. [1] Cyclodial Propeller의 경우 다양한 요인들에 의해 낮은 Rotational Speed에서 높 은 추력을 얻어낼 수 있는데, 이 특징 덕에 대표적인 VTOL (Vertical Take Off and Landing)인 헬리콥터의 단점인 Retreating Blade Stall을 해결 가능하다. 헬리콥터의 날개는 헬리콥터의 진행방향과 동일한

방향으로 갈 때와 반대의 방향으로 가는 시점이 헬리콥 터의 Sagittal plane을 기준으로 나뉘게 된다. 진행방향 의 유체 속도로 인해, 헬기 진행 방향과 반대의 방향으 로 가는 날개는 더 느린 Blade 상대 유체 속도를 가지 게 된다. 더 느린 속도는 Lift Equation에 의해 더 낮은 추력을 갖게 되고, 저하된 추력을 상쇄하기 위해 비행 사는 헬리콥터 Blade의 AoA (Angle of Attack)을 증 가시키게 된다. 하지만, 일정 AoA 이후에는 Flow Separature로 인해 Stall Angle에 도달하게 되고, 추력 이 급격하게 떨어지게 된다. 이러한 위험한 상황을 Retreating Blade Stall이라 칭하며, 이로 인해 헬리콥 터는 전진 속도에 제한이 있다. 하지만 로터의 회전속 도가 빠르지 않은 Cyclorotor에서는 이러한 문제가 자 연적으로 해결되어 더 높은 전진속도를 가질 수 있다. Symmetric Thrust : Cyclodial Propeller는 특이적인 구조 덕분에 유체에

대한 상대속도가 모두 같다는 장점이 있다. 일반적인 Propeller의 경우 중심에 대한 거리의 함수로 공기와 접하는 속력이 달라 발생하는 추력도 다르고 그로 인해 날개가 휘는 문제가 있어 설계가 복잡하다는 단점이 있 다. Cyclodial Propeller는 이러한 문제점 없이 간단한 Airfoil 설계로 높은 효율을 얻어낼 수 있다. Delay of Blade Stall : Cyclodial Propeller에서의 날개는 Pitcher를 통해

떨어진 이심축을 기준으로 회전하는 Flaparm에 연결되 어 회전하면서 Pitching이 되기 때문에 1회전당 2번 Pitching Motion이 일어나게 되면서 Pendulum Motion 과 같이 날개의 Pitching Motion이 표현된다. 이러한 특성으로 인해 날개의 AoA가 급격하게 증가

하고 감소하면서 규칙적이나 반복적인 Lift를 발생시켜 Stall을 지연시킨다. 이 덕에 더 높은 Stall Angle을 가 지게 되어 높은 Advance Ratio에 기여한다. Noise : 낮은 회전속도로 인해 더 적은 소음이 발생한다. 일

반적인 프로펠러의 경우 Propeller Tip의 속도가 음속 을 초과하게 되는 순간 저항이 급격하게 증가하여 엄청 난 소음이 발생하지만 Cyclodial Propeller는 작은 회 전속도로 이러한 고려사항에서 자유롭다.

1.1.2 Cyclodial Propeller의 단점 : Blade을 지지하는 Spoke가 같이 회전할 수 밖에 없

는데 이러한 Spoke에서 어쩔수 없이 필연적으로 발생 하는 Drag이 존재한다. 또한, Blade들이 원심력을 많이 받게 되는 구조로 크기와 강성에 비해 엄청나게 낮은 무게를 가져야 한다. [2]

1.2 Wing Fence : 스웹트 날개(swept-wing) 항공기가 저속으로 비행

할 때, 날개의 전방 모서리 각도로 인해 일부 공기 흐 름이 횡방향으로, 즉 날개 끝 쪽으로 이동하게 된다. 날 개 중앙 부근의 공기 흐름은 전방 모서리 각도뿐만 아 니라 날개 뿌리로부터의 횡방향 공기 흐름에 영향을 받 는다. 이로 인해 날개 끝에서는 공기 흐름이 거의 모두 횡방향으로 이동하게 되어, 추력에 기여하는 효과적인 유체의 양이 크게 감소해 날개의 추력이 감소하게 된다. 이런 문제를 해결하기 위해 'Wing Fence'의 도입이

필요하다. 'Wing Fence'는 공기 흐름이 너무 멀리 이동 하거나 속도가 빨라져 전체 날개가 한번에 기능을 상실 하는 것을 방지하는 역할을 한다. Cyclodial Propeller 에서 또한, 날개 양 끝단에서 발생하는 횡방향 모멘텀 을 올바르게 제어하고 추진하기 위해서는 Wing fence 의 구조가 필요하다. 1.3 Wingtip device Wingtip device는 Fixed Wing Aircraft에서 Drag을

감소시켜 추력효율을 증가시키기 위해 도입하는 장치이 다. 날개가 위로 향하는 추력을 만들어낼 때, 날개의 아 랫면은 상대적으로 고기압, 윗면은 저기압으로 유지되 게 된다. 이때, 날개가 있는 면에서는 괜찮지만 날개의 횡방향으로 끝나는 지점에 근접해서는 아랫면의 고기압 유체가 윗면의 저기압 지역으로 이동하면서 회전하게 된다. 이렇게 형성되는 와류를 Wingtip Vortice라고 하 며, 다른 항공기의 안전을 위협하며 항공기의 Drag을 감소시키는 요소이다. Wingtip Device는 날개의 끝단에 이러한 와류 형성을 막는 벽면 또는 장치를 부착하여 Wingtip Vortice를 감소시키는 것이다. [3]

Fig. 2 : Wingtip Vortice, [3]
1.4 Relative Curvature Effect P.G. Milgliore 등(2012)에 따르면, Darrieus

turbine blade의 공기역학적 특성에는 유체 흐름의 곡 률이 중요한 영향을 끼친다. Darrieus turbine은 cyclorotor와 마찬가지로 익형 구조의 날개를 어떤 축 주위로 회전할 수 있도록 하는 풍력 발전기이다. 이때 각각의 날개는 곡선 운동을 하게 되는데, 이 때

문에 실제보다 캠버(camber)가 큰 (익형의 휘어진 정도가 큰) 효과가 발생한다고 한다. 이를 virtual
camber | effect라 | 한다. | 해당 | 논문에서는 | 이를
conformal mapping technique를 이용하여 표현한다. 또한 virtual camber effect의 conformal mapping을

- 3 -

나타낸 Fig. 3에서 보이는 바와 같이 받음각(Angle of Attack, AoA)이 증가하는 효과도 있다. [4]


Fig. 3 : Virtual Camber Effect of Rotating Airfoil [4]

본 연구에서는 Wing Fence와 Relative Curvature라 는 두 가지 새로운 개념을 Cycloidal Propeller에 적용 하여 그 성능을 개선하고자 하는 것이 본 연구의 주요 동기이다. 이때, 본 연구에서 적용한 Wing Fence는 Wingtip

Device로의 효과 또한 존재하여 두 가지 목적 모두로 해석하기 위해 Wingtip Device에 대한 내용 또한 첨부

### 하였다. 2. 연구 방법 및 이론

1. 가설과 가설에 대한 근거 1.1 Wing Fence에 관련한 가설 (WF로 축약) WF-1 WF를 적용하면, Lift Coefficient가 증가하게 된

다. Durga Priya.G 등 (2016)에 따르면, 일반적인 Glider 의 날개에 Wing Fence를 적용하였을 때, Stalling Angle의 증가와 Lift Coefficient를 30%가량 증가시키는데에 도움 을 주었으며, 약간의 Drag Coefficient 증가가 있었지만 전체적으로 Lift to Drag Ratio는 증가했음을 알 수 있다. Cyclodial Propeller와 같이 회전하는 구조에서도 비슷한

작용을 할 것이라 기대 가능 하다. [5]

WF-2 WF를 적용하면, Wingtip Vortice가 감소하여
Drag이 | 감소한다. | 우리가 | 실험에서 | 적용하게 | 될
WingFence는 Wingtip Device 로의 작용 또한 할 수 있 어, Wingtip Vortice를 감소 시킬 수 있다. 이로 인해 유발 되는 Wingtip Vortice Drag이 감소할 것으로 예상된다. WF-3 WF를 적용하면, 추력이 증가한다. 위의 WF-1

와 WF-2가 성립함으로 인해 추력이 증가할 것으로 예상 된다. WF-4 WF를 적용하면, 동일 추력 대비 소음이 감소한

다. 동일 추력일 때 필요한 Blade Speed하고 Watt가 감 소하여 소음이 감소할 것으로 예상된다.

1.2 Relative Curvature 에 대한 가설 (RC로 축약)

RC-1 RC를 적용하면, Drag이 감소한다. Flow Curvature 이론에 의해, Propeller에 대한 유체의 이동 경로와 동일한 형태의 프로펠러를 적용하면 Drag을 감 소시킬 수 있다. Cycloidal propeller의 회전 반경과 같 은 곡률 반지름의 날개를 이용할 경우, 날개 주위의 유 속이 rectilinear flow의 모양을 따르도록 conformal mapping을 하면 angle of attack이 0인 상황과 대응되 며, drag force가 최소이다. 따라서 날개가 지면과 수직 인 방향으로 이동할 때도 virtual camber effect에 의해 drag가 생성되는 편평한 날개에 비해 곡률 반지름이 날개의 회전 반경과 일치하는 날개가 에너지 관점에서 더 효율적일 것이다. RC-2 RC를 적용하면, 추력 효율이 증가한다. 추력

이 발생하지 않는 구역에서의 Drag이 감소하여 추력 효율이 증가할 것이다. 날개 자체가 휘어져 있으면 virtual camber effect 외에도 날개에 camber가 있는 효과가 있어 날개가 cycloidal propeller의 위, 아래쪽 에 있을 때 받는 양력이 더 클 것이다. RC-3 RC를 적용하면 소음이 감소한다. Drag의 감소

로 인해 소음이 감소할 것이다. 2. 파이썬을 이용한 Flap Angle Distribution 찾기 Flap의 각도는 주회전축과 이심축 사이 거리, 날개의

반지름, Flap 고정축간 거리에 의해 결정된다. 하지만 이 관계가 비선형적이기 때문에, 파이썬을 이용해 각도 분배를 찾았다. 아래는 이를 찾기 위한 좌표평면상 좌표 정의이다.


Fig. 4 : 좌표평면 상 거리에 대한 정의
l : Flap에서 두 고정축 간 거리 (두 축은 회전 가능 함). 20mm로 설계되었다. L : 주회전축과 Flap이 고정되는 축 사이 거리. CenterArm과 FlapArm 모두 75mm 길이로 설계되었

다.d : Pitch Distance, 주회전축과 이심축 간 거리, 본

설계에서는 이 거리를 Variable Pitcher로 바꾸어가면 서 활용한다. 그러나, 날개가 정확히 중심에 연결된 것이 아니기

- 4 -

때문에 여기서 보여지는 Pitch Angle에는 오차가 포함 되어 있다. Flap Rotational Axis에서 접하는 직선을 기 준으로 AoA를 정하게 되면, 양 또는 음의 편향을 갖게 AoA 결과가 나오기 때문에 이를 포함해서 계산해주어 야 한다. 이를 포함한 AoA는 Airfoil의 Chord 상 중심 에서 회전반경의 접선을 기준 0도로 사용하였다. 아래에서는 실험에서 사용한 Pitch Distance 인

6mm, 8mm, 11mm, 13mm에 대한 결과 분석을 하였다. 0mm에 대한 데이터를 통해 AoA (Angle of Attack)보

정을 수행하였다. Fig 5에서 Angle of Spoke는 Flap Rotational Axis와

연결된 Mainframe과 Mainframe 회전시 어떠한 고정 된 방향 (회전축과 수직한 벡터) 사이의 각도이다.


Fig. 5 : AoA Graph by Pitch Distance


Fig. 6 : Max AoA by Pitch Distance

Flaparm으로 인해 일어나는 Pitching Motion은 거의 단조화 운동의 개형을 따른다고 볼 수 있으며, Pitch Distance가 커짐에 따라 Max AoA 또한 훨씬 커진다 는 것을 알 수 있다. 이때, Max AoA의 최소가 6mm Distance에서 17.29 deg 인 것을 확인 할 수 있는데, 이는 일반적인 Rectilinear Flow 에서는 이미 한참

Stall | Angle을 | 넘은 | 수치이다. | 이는 | Cyclodial
Propeller의 특징으로 높은 Stall Angle을 가진다는 특 성에 의한 것이다. 3. Relative Curvature Code NACA Airfoil을 Csv로 저장하게 되면, 각 점이

Chord 방향의 x좌표와 Chord에서 수직한 방향으로 뻗 은 위와 아래 점으로 표현되는 것을 확인할 수 있다. 본 연구에서 사용한 Relative Curvature Mapping

Method는 회전반경의 둘레로 Chord를 맵핑하는 것이 다. Chord이 회전반경 둘레를 따라 굽었다고 가정하고, 해당 원의 점에서 접선에 수직하게 위 아래만큼 이동하

여 점을 찍는 방식이다. 가장 간단하면서 연구에서 추 구하는 대상을 얻을 수 있는 방식이다.

4. WF와 RC를 적용한 Cyclodial Propeller의 검증 4.1 Cyclodial Propeller 실험의 설계 4.1.1 전체 설계에 대한 참고 : Jude Schauer의 Cyclodial Propeller 연구를 참고하여, 베어링을 이용한 간단한 조립방식을 적용하여 설계하였으

며 Mainframe Radius하고 날개의 Chord, Wingspan을 적
용했다. | Jude | Schauer의 | Cyclodial | Propeller는
3000RPM에서 328g의 Thrust를 만들어 낼 수 있으며 일반적인 프로펠러의 중량비와 맞먹을정도로 경량화에 성
공했다. | Thrust to Weight Ratio 4.69:1, 일반적인
Cyclorotor의 | 2배의 | 수치를 | 달성하였으며, | 328g의
Thrust를 78W에서 뽑아내어 4g/W이라는 수치를 얻어내 었다. [6]

4.1.2 Airfoil의 설계 Airfoil은 적절한 두께를 가지며 Camber 되어있지

않은 NACA 0012 Airfoil을 기준으로 테스트하였다. Chord 50mm, Wingspan 150mm로 설계하였다. 출력시

에 두께는 1mm로 하여 출력하였다. 위키백과에 | 따르면, | 대부분의 | Airfoil의

Aerodynamic Center는 Chordwise 1/4 부근에 위치한
다고 | 한다. | Flapar이 | 마운팅되는 | 위치는 | Flap
Rotational Axis에서 20mm 떨어진 곳에 설계하였다. 즉, 첫째 구멍은 Chord에서 12.5mm 떨어진 곳에 위

치하고, 두 번쨰 구멍은 그 이후 20mm 떨어진 Chord 위에 중심이 존재한다. Wing Fence의 경우, Airfoil당 두 개씩, 양 끝단에서 3mm 떨어진 곳에서부터 1mm 만큼 두꺼운 Wing Fence를 만들었다. Wing Fence는 전체 Airfoil을 5mm 만큼 간격띄우기 해서 (Airfoil의 표면으로부터 5mm만큼 수직하게 떨어진 점들의 집합) 만들었다.


Fig. 7 : Airfoil Designs in Fusion 360, Straight, Curved, WF versions

- 5 -

사용하고 테스트한 날개의 종류는, NACA 0012 Straight, No WF // NACA 0012 Straight, WF // NACA 0012 Curved, No WF // NACA 0012 Curved WF, 이 렇게 총 4가지에 대해서 실험하였다. 이 중심에 Insert하고 M2 나사, 순간접착제를 이용

하여 구조물을 고정하고, 윤활유를 발라 회전할 수 있 도록 하였다. 베어링은 682OP 베어링을 사용하였다. 4.1.3 Cyclodial Propeller의 설계


Fig. 8 : Mainframe, Flaparm, Full Assembly
Variable | Pitcher의 | 설계. | Pitcher는 | Rotor
Rotational Axis와 Flaparm Rotational Axis를 연결해
주는 | 장치로, | Cyclodial | Rotor의 | Pitching
Characteristic을 결정짓는 중요한 요소이다. 이때, Pitch Distance를 한 번에 쉽게 조절 가능하도록

Variable Pitcher를 설계하게 되었다.


Fig. 9 : Variable Pitcher의 설계
4.1.4 Thrust Stand의 설계와 측정 변인의 측정 도구 Thrust Stand는 카본 파이버 파이프 (4-6mm)와 3D

프린팅으로 만든 결합 부품들로 제작하여 테이블에 절연
테이프로 | 부착하였다. | Load | Cell과 | Motor | Stand,
Propeller Mount, Tachometer Sensor Mount의 기능을 전부 다 할 수 있도록, 간단한 실험 장비를 만들었다.


Fig. 10 : Load Cell & Motor, Tachometer, dB Measure, Watt measure

모터는 MT2213 모터를 사용하였으며, GT2 300T Closed Pulley를 이용하여 풀리와 연결지었다. 그 이외 측 정 도구들은 위에 프로펠러 실험 시 사용한 도구랑 일치 한다. 실험 시 바꾸어가며 실험한 변수는 Power Value to ESC, Pitch Distance, Airfoil Type을 바꾸어가며 실험하 였으며 이때 측정한 값으로는 RPM, 소음 (dB), Power (W)을 측정하였다.


Fig. 11 : 실험한 Airfoil들을 가지고 조립한 Cyclodial Rotor의 모습. 4.1.5 Propeller Test 실제 프로펠러에 비해서 실질적으로 더 좋은 성능을 낼

수 있는지 대조하기 위해 MT2213 모터에 가장 대중적으 로 사용되는 10인치 프로펠러를 사용하여, RPM, 소리 (dB), Power(W), Thrust(g)을 측정하였다. 프로펠러의 모델은 1045 Prop이며 중형 이상의 멀티콥터에 가장 흔 하게 사용되는 로터이다.


Fig. 12 : Propeller Thrust Stand의 모습. Load cell, Motor, IR Sensor, Propeller와 이들의 지지대로 구성되어있다. RPM은 적외선 장애물 센서와 아두이노의 인터럽트

를 이용하여 측정하였으며, 간이 타코미터로 꽤 정밀하 게 측정 가능했다. 소리의 크기는 LUAZ-320이란 데 시벨 측정기를 이용하여 60cm 거리에서 측정하였다. Power는 시중에서 판매되는 200A High Precision

Watt Meter를 이용하여 측정하였으며, Thrust는 1kg Load Cell과 Hx711을 연결하여 아두이노를 통해 측정 하였다.


- 6 -
3. 결과 3.1 Propeller Test 결과 : 프로펠러에 대해서는 Thrust Value 17개에 대하여

904~4496 RPM까지 Thrust (g), Power (W), Noise (dB)를 측정하였으며, 다음 데이터를 첨부한다. 4496rpm, 39.6W에서 337g의 추력을 만들어냈으며

이때 소음은 81.5dB였다. 최대 추력을 발생시킬 때 Thrust Per Watt (g/W) Ratio는 8.51이었으며 모든 측 정치에서 최대치는 11.54 g/W 였다. Max Thrust per Watt 에서 2213Rpm, 6.5W에 75g의 Thrust를 만들 었으며 71.4dB를 기록하였다. 이 데이터는 모터와 프로펠러 제조사에서 제공한 정

보와 잘 들어맞아 실험이 잘 진행되었음을 알 수 있다. 3.2 Cyclodial Propeller 실험 결과 :

Pitch Distance (6mm, 8mm, 11mm, 13mm), 날개 5가지, Thrust Value 20개씩에 대해 4개의 변량을 측 정을 하였기 때문에 데이터의 수가 총 약 1280개로 너 무 많아 분석에 필수적인 특징들로 가공하여 첨부한다. 어떠한 프로펠러가 성능적으로 좋다고 말하기 위해

서는, 추력, 에너지 효율, 소음이 모두 좋아야 한다. 이 러한 세 조건을 만족시키는 프로펠러를 수치적으로 찾 기 위해 아래와 같은 수치들을 제시하고 그를 요약하여 정리하였다. CD : Drag Coefficient. 일반적인 항공기에서는

=

(2) 로 표현된다. 본 연구에서는 오로지

받는 힘과 각속도만 변하므로, 이에 비례할 것이라고 판단되는 Watt / rpm^2 (3)으로 Drag Coefficient에 대해 분석하였다. CL : Lift Coefficient. 위의 서론에서 언급하였으며 본

연구에서는 Thrust / rpm^2으로 상호 대조를 수행했 다. Max thrust : 최대 추력과 최대 추력일 때의 g/W, CD,

dB를 조사한다. Max efficiency : 최대 추력 효율을 가질 때의 추력과

CD, dB를 조사한다. Max Lift Coefficient : 실험에서 각속도가 변함에 따

라 CL의 변화가 무의미하게 작아, 최대치로 기입하였 다. 아래에서 언급되는 Thrust의 단위는 모두 gram이며, x축에 Cyclodial Propeller의 Variable Pitcher로 조작

한 Pitch Distance를 기준으로 그래프를 그렸다.

Fig. 13 : NACA 0012 Straight

Fig. 14 : NACA 0012 Straight WF

Fig. 15 : NACA 0012 Curved

Fig. 16 : NACA 0012 Curved WF


- 7 -
4. 고찰 (Discussion) WF –1 Lift Coefficient 증가 :

Fig. 17 : Straight Airfoil에 WF를 적용하였을 때, Max Lift Coefficient의 증가율

Fig. 18 : Graph of Curved vs CurvedWF Lift Coefficient

위의 결과에 따르면, Straight Version의 경우 8mm 와 11mm의 Pitch Distance에서 각각 161%와 168% 의 Lift Coefficient 증가가 있었음을 확인 할 수 있으 며, RC 적용 Curved Version의 경우에는 6mm와 8mm의 Pitch Distance에서 각각 129%와 128%의 Lift Coefficient 증가가 있었음을 확인 가능하다. 비록 전 구간에서 확실한 효과가 있는 것은 아니지만 대체로 좋은 효과를 보여준다고 요약할 수 있으며 Straight Version에서는 엄청난 성능 증가를 가져다줌을 볼 수 있다. WF-2 WF를 적용하면, Drag이 감소한다. CD at Max thrust, CD at Max Efficiency


Fig. 19 : Straight 와 Curved Airfoil에 WF 적용 시 Max Thrust 에서 Drag Coefficient 변화율

Fig. 20 : Straight 와 Curved Airfoil에 WF 적용 시 Max Thrust Efficiency에서 Drag Coefficient 변화율
Drag Coefficient의 변화는 Wing Fence의 유무하고 별로 관계가 없다는 것을 확인할 수 있다. 이는 선행 연구 (Rectilinear Flow에서 Glider 날개에 Wing Fence 적용 연구)에서 보인 것이랑 같으며, 약간의 Drag Coefficient 증가가 있다고 한 것이랑 일치한다. 따라서 Wingtip Vortice 감소로 인한 Drag 감소 효과

는 미미하다고 요약 할 수 있다. WF-3 WF를 적용하면, 추력이 증가한다.

Fig. 21 : Straight Airfoil에 Wing Fence 적용 시, Max Thrust, Thrust at Max Efficiency, Max Efficiency의 변화율

Fig. 22 : Curved Airfoil에 Wing Fence 적용 시, Max Thrust, Thrust at Max Efficiency, Max Efficiency의 변화율 Straight Version와 RC를 적용한 Curved Airfoil 두 가지의 차이가 확연하게 드러난다. Straight Version에 서는 확실하게 WF-3 가설이 성립하고, 엄청난 효과를 보여준다. 그러나, Curved Version에서는 그 효과가 미 미하고 상관이 없어 보인다. Wing Fence를 적용하게 되면, Straight Airfoil의 경

우 확실하게 최대 추력이 증가하고, 최대 효율에서의 추력이 증가하는 경향이 있으며, Pitch Distance 최적화 시에는 최대 효율까지 40% 증가하였다. 최적의 결과를 보인 8mm Straight WF Airfoil의 경우, 최대 추력이 8mm Straight Airfoil에 대비하여 65%, 최대 효율에서 의 추력 122%, 최대 효율이 40%나 증가하였음을 알 수 있다.


- 8 -

WF-4 WF를 적용하면, 동일 추력 대비 소음이 감소한다.

Fig. 23 : WF 적용시, Curvature 적용 유무에 따라 동일 추 력에서의 DB 변화율

Straight와 Curved Airfoil에 대해, Wing Fence가 있고 없는 모델 중에서 더 적은 최고 추력을 가지는 추
력을 | 기준으로 | 하여 | 데시벨을 | 대조하였다. | 이때, Straight Airfoil의 경우 Pitch Distance가 큰 절반에서

는 소음 감소 효과를 가졌고, Pitch Distance가 작은 절 반에서는 반대로 소음이 증가하였다. 반면, Curved Airfoil의 경우 전반적으로 조금 감소하거나 그대로였다. RC-1 RC를 적용하면, Drag이 감소한다.

Fig. 24 : Relative Curvature 적용 시 Max Thrust 에서의 CD 변화

Fig. 25 : RC 적용 시 Max Efficiency에서 CD 변화

11mm Straight vs Curved를 제외하면 전체적으로 감소한다는 것을 알 수 있다. 따라서 RC-1은 대체로 성립한다고 볼 수 있다. Relative Curvature는 Drag을 감소시키는데 기여한다.

RC-2 : RC를 적용하면, 추력 효율이 증가한다.

Fig. 26 : RC 적용 시 Max Efficiency (g/W)의 변화율

Wing Fence가 없을때에, 낮은 Pitch Distance에서는 확연한 최대 추력효율 증가에 도움이 되지만, 13mm에 서는 확연하게 감소된다. 이는 Relative Curvature 적 용시에 위 아래에서 원래 상하 대칭적이었던 Airfoil Pitch 형상이 Curvature로 인해 달라지게 되면서 효율 이 감소한 것으로 추정된다. Wing Fence 적용시에는 확실하게 최대 추력효율을

감소시킨다. Drag Coefficient의 감소에도 불구하고 추 력 효율이 감소했다는 것은 Lifting Factor가 크게 감소 하게 되었다는 것을 의미한다. 따라서 RC는 Drag 감소 에는 도움이 되지만 Lifting Factor까지 감소시키는 요 소라고 결론지을 수 있다. RC-3 RC를 적용하면 소음이 감소한다. 아래 표는, 가장 추력효율이 높은 순간에 dB을 모은

이후, Curvature를 적용하여 얼만큼의 dB 변화가 있었 는지를 나타내는 표이다. 단위는 dB이다.

Fig. 27 : Pitch Distance에 따라, RC를 적용하였을 때 RC 없는 모델에 비한 Decibel 변화량

위 표에 의하면, 추력효율이 높은 순간에 dB은 모두 증가하였음을 확인할 수 있으며, 심지어 매우 큰 폭으 로 증가하였다. 이는 감소한 CL로 인해 동일한 추력을 내기 위해 더 빠른 회전수가 요구되었기 때문으로 해석 된다.

Pitch Distance | Thrust Value | No WF | WF | DB Change
6mm | 25g | 66.5dB | 74.5dB | 8.0dB
8mm | 48g | 69.6dB | 74.4dB | 4.8dB
11mm | 60g | 77.7dB | 71.2dB | -6.5dB
13mm | 62g | 77.9dB | 76.0dB | -1.9dB
Curved | 6mm | 26g | 75.8dB | 76.1dB | 0.3dB
| 8mm | 60g | 76.4dB | 74.0dB | -2.4dB
| 11mm | 81g | 78.3dB | 76.0dB | -2.3dB
| 13mm | 84g | 79.0dB | 79.0dB | 0.0dB

Straight

RC 적용시 Thrust Efficiency 증가율 | 6mm | 8mm | 11mm | 13mm
No WF | 8% | 15% | 1% | -15% WF | -19% | -7% | -9% | -12%
Pitch Distance | 6mm | 8mm | 11mm | 13mm
No WF | 10.4dB | 11.3dB | 12.8dB | 8.9dB
WF | 1.0dB | 1.2dB | 7.6dB | 7.7dB

- 9 -
5. 결론(CONCLUSION) WF-1, Lift Coefficient의 증가 : Straight Version의

경우 8mm와 11mm의 Pitch Distance에서 각각 161% 와 168%의 Lift Coefficient 증가가 있었음을 확인 할 수 있으며, RC 적용 Curved Version의 경우에는 6mm 와 8mm의 Pitch Distance에서 각각 129%와 128%의 Lift Coefficient 증가가 있었다. 전 구간에서 증가하는 결과를 얻은 것은 아니지만 대체로 성립한다. WF-2, Drag의 감소 : Cyclodial Propeller에 Wing

Fence를 부착하는 것은 Drag Coefficient 감소에 도움 이 되지 않으며, 실험 결과에서는 대체로 무관한 경향 을 보였다. WF-3, Lift의 증가 : Straight Airfoil의 경우 확실하

게 최대 추력이 증가하고, 최대 효율에서의 추력이 증 가하는 경향이 있으며, Pitch Distance 최적화 시에는
최대 | 추력 | 효율까지 | 40% | 증가하였다. | 따라서
Cyclodial Propeller에 Wing Fence를 적용하는 것은 확실한 추력 상승을 일으키며 추력 효율까지 증가시킬 수 있다. WF-4, 소음 감소 : Wing Fence를 사용하는 것은 동
일 추력에서 약간의 소음 감소에 도움이 될 수 있다. RC-1, | Drag의 | 감소 | : | Relative | Curvature를

Cyclodial Propeller에 적용해 로터 반지름과 같은 반 경으로 회전 맵핑시키게 되면 최대 24%까지 Drag Coefficient를 감소시킨다. 따라서, Relative Curvature 의 적용은 대부분의 경우에서 Drag Coefficient를 감소 시킬 수 있다. RC-2, 추력 효율의 증가 : Relative Curvature를

Cyclodial Propeller에 적용하면, 추력 효율이 증가하지 않는다. RC-3, 소음 감소 : Relative Curvature를 사용하는

것은 동일 추력에서 소음을 증가시킨다. 프로펠러와의 대조 : 전체적으로 추력 효율과 최대 추력에서 아직 크게

밀리지만, 이는 해당 모터에 최적화된 설계가 아닌 실 험을 위한 설계로 인해 그런 것이다. 소음 면에서는 아 무리 시끄러워도 프로펠러의 소음인 81.5dB를 넘지 못 하였다. 동일 추력에서의 소음 또한 최적의 Cyclodial Propeller (Pitch Distance 8~11mm, StraightWF) 유 사하거나 더 낮게 나왔다. 따라서 소음과 기동성 면에 서 프로펠러보다 더 월등한 프로펠러를 만드는데 성공 하였다고 판단할 수 있다. 프로펠러는 직경이 커질수록 추력 효율이 급격하게 상승하는데, 이는 사용가능한 공 기의 면적이 넓어짐으로 인한 것이다. 본 연구에서 비 교대상으로 사용한 1045 propeller는 직경이 10인치로, 큰 편에 속하지만 직경이 훨씬 작은 6x3 프로펠러의

경우 최대 추력 효율이 4.7g/W으로 알려져 있다. 따라 서, 크기의 제한으로 인해 추력효율이 급변하는 프로펠 러와 대조하여 경쟁력이 있을 것으로 생각된다.

6. 제언

전 Pitch Distance 구간에서 뚜렷한 Lift Coefficient 증가를 보이지 않는 이유는 날개의 Pitch가 계속해서 바뀌기 때문으로 추측한다. 이러한 내용은 차후 연구를 통해 연구하고 싶다. Cyclodial Propeller의 실제 적용 을 위해서는 경량화 방법과 손쉬운 조립 방식에 대한 다양한 모색이 이루어져야 한다. RC 적용 된 Airfoil에 서 추력이 감소하는 원인 또한 이론적으로 검토 해보고 싶다. 아래로, Cyclodial Propeller의 경량화를 적용하여 더

빠른 회전수에서 Wing Fence와 Relative Curvature의 성능을 살펴보고자 한 연구 내용을 기록하겠다. 1 : Foam Cutting Method 폼보드를 Airfoil 단면을 가지며 150mm 길이를 가

지는 Airfoil로 가공한다는 것은 결코 쉽지 않다. 이러 한 한계를 극복하기 위해 다양한 방법을 모색하였으며 실행 중에 있다. Foam – 1 : Jude Schauer의 연구에서는 이러한 방식으로 Foam

을 가공하였다. Airfoil의 둘레와 같은 형상의 얇은 3D 프린트된 구조물을 출력한 이후, 이 구조물의 위에 Airfoil 둘레와 일치하게 열선을 두른다. 열선에 열을 가하면서 3D 프린트 구조물을 폼보드에 퉁과시키면, 3D 프린트 안에 Airfoil 형상의 Airfoil이 남게 된다. Foam – 2 : Airfoil 단면 형상의 레이저 컷팅 된 나무판을

150mm 폭의 폼보드에 부착 또는 고정시킨 이후, 폼보 드를 무게를 이용하여 고정시킨다. 그 이후, 열선은 레 이저 컷팅 나무판을 자르지 못하므로 그 둘레를 따라 이동시킬 수 있다. Airfoil이 더욱 두꺼운 경우에는 시 도해볼만 하나, Chord가 50mm인 작은 Airfoil에서는 정밀하게 자르기 쉽지 않았으며 약간 불규칙하게 뽑히 기도 하였다. 2 : LW-PLA LW PLA는 Foaming Material을 3D printing

Filament에 넣어 경량 부품들을 출력하기 좋게 한 것 이다. 이때, 일반적인 PLA에 비하여 약 0.45배의 무게 로 감소시킬 수 있으며 이는 다양한 Airfoil 구조를 탐 색하고 실행하는데 큰 이점을 주게 된다. 허나 LW PLA는 알려진 몇 개의 고질적인 문제들로 인해 깔끔 한 출력을 위해서는 많은 신경을 써야 하며, 그러하여 상세한 출력 세팅에 대한 정보를 기재하였다. 첫째로, 발포하는데 시간이 걸리며 3D 프린터 노즐

에 의해 충분히 열에너지를 흡수할 시간을 가져야 해서 느린 프린트 속도를 필요로 한다. 대부분 제조사에 의 하면 40~100mm/s의 속도를 제공하지만, 본 연구에는 시행착오 이후 20mm/s에서 가장 높은 퀄리티의 출력 물이 나온다는 것을 확인하였다. 둘째로, Stringing이 일어나게 된다. Stringing이란, FDM 3D 프린팅 시 노즐에서 필라멘트가 출력되다가, 완전히 끊어진 다른 경로로 이동하게 되는 과정에서 필

라멘트 Extrusion이 완전히 멈추지 않고 지속되어 거 미줄과 같은 형상을 이루게 되는 문제를 뜻한다. LW PLA에서 Stringing이 유독 심한 이유는 발포 특징 때 문이며, 제조사에서도 이 점을 감안하라고 한다.


- 10 -

이러한 문제를 해결하기 위해서는 전체 출력시에 단일 경로로 출력하는 방법이 필요하였고, 이를 구현해둔 Vase Mode이라는 셋팅이 존재하였다. Vase mode에서는 나선형 구조로 전체 구조물을 단일한 경로로 출력하여 깔끔한 외 관을 가진다. Vase Mode에서는 적층 간 시간이 매우 짧아 졌기 때문에 (노즐과 출력물의 충돌로 한 번에 한 개의 Airfoil만 출력할 수 있음) 20mm/s 로 출력해야 했고, 출력 의 두께인 Layer Width는 0.6에서 0.8, Layer Height는 0.3mm 로 출력하였을 때 깔끔한 결과를 가져다주었다. 출 력은 Bambulab X1C 0.4mm Nozzle로 진행하였으며, LW-PLA의 이름은 덕유항공의 ePLA-LW이다. 본 연구에서는 위 방법들 중 LW PLA 경량화 방식

을 실험해보고자, LW-PLA로 출력된 경량 Airfoil을 접목하여 실험을 진행하였으나, Airfoil의 강성이 부족 하여 회전하면서 휘어 추력 효율과 추력이 심각하게 감 소하는 현상이 관찰되었다.


Fig. 28 : LW PLA를 적용한 Straight WF Airfoil Test 모습

Fig. 29 : Straight WF LW-PLA Results

Fig. 23 : Straight WF Airfoil에 LW-PLA 변경 시 성능 변 화 (Max Thrust, Efficiency at Max Thrust)
Fig 30에 따르면 전체적으로 모든 성능이 감소하였음 을 볼 수 있다. Airfoil의 무게가 14g에서 3g 정도로 감 소하였음에도 추력 효율이 감소하였다는 점을 본다면, 이는 확연하게 Airfoil의 형태가 원심력으로 인해 휘었

다는 것을 알 수 있다. 따라서, 경량화도 필요하지만 경 량화와 동시에 강성을 유지하여 형상이 바뀌지 않도록 제어하는 것 또한 매우 중요함을 알 수 있었다.

향후 연구에서는 Carbon Fiber, Foam Board, Light Weight PLA등 다양한 소재와 방식을 접목하여 Wing Fence가 부착된 경량 설계의 프로펠러와 맞먹을 수 있는
Cyclodial Propeller를 개발하고자 한다. References
[1] Wikipedia, Advance Ratio, https://en.wikipedia.org/wiki/Advance_ratio, 2023, (Accessed Sep.,10, 2023)
[2] Wikipedia, Cyclorotor, https://en.wikipedia.org/wiki/Cyclorotor, 2023, (Accessed Sep.,10, 2023)
[3] Wikipedia, Wingtip Device https://en.wikipedia.org/wiki/Wingtip_device, 2023, (Accessed Sep.,10, 2023)
[4] P. G. Migliore, W. P. Wolfe and J. B. Fanucci, Flow Curvature Effects on Darrieus Turbine Blade Aerodynamics, Published Online:23 May 2012, pp 49-55
[5] Durga Priya.G, D.V.Balaji, Stall Characteristics Study of Aircraft Wing with Fence, pp 793-794, International Journal of Engineering Research & Technology (IJERT), 2016
[6] Jude Schauer, The Cyclorotor Is Now a Match For Propellers! ,
https://youtu.be/wp1xkuKjN_Y?si=8z9UAKtrSKfmtEfG, 2022 (Accessed Sep.,10, 2023)

조용우(Yongwoo Cho)

2022년 2월 : 서일중학교 졸업
2022년 3월~현재 : 서울과학고등
학교 재학
2023년 7월 : 서울과학고등학교 과
제연구 물리과 최우수상
2023년 8월 : 한화사이언스챌린지
2023 대상 수상
2023년 9월 : 김천시 전국무한상상
탐구토론대회 최우수상
2023년 10월 : 서울과학전람회 예선
최우수상
<관심분야>
기계공학, 로봇공학, 컴퓨터공학

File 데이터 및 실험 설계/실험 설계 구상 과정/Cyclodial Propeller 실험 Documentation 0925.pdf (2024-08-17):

## Cyclodial Propeller 실험 Documentation

조용우

개요 ;

Cyclodial Propeller 개발을 위한 모든 실험을 상세히 적는다. 전체 흐름 및 실험 구성

### 0. Test Stand Verification

0-1 : RPM Meter
0-2 : Thrust

### 1. 기본 프로펠러 분석

1-1 : 프로펠러를 정지한 유체 속에서 가동시키면서 RPM (회전수), Thrust, 소음, Power를 측정한다. 2. 기본 Cyclodial Propeller 분석

2-1 : Default Cyclodial Propeller를 다양한 유속과 각도 속에서 가동시키면서 RPM (회전수), Thrust, 소음, Power를 측정한다. 2-2 : Relative Curvature를 적용한 회전체와 그렇지 못한 회전체의 RPM 감쇠 속도를

### 비교한다. 3. Flap (Wing Fence) 분석

3-1 : 각 날개를 풍동실에 넣어, 유속, 회전각, 받음각을 변수로 하여 테스트한다. 이때, 회전각과 받음각, 유속은 자동화된 실험장치를 이용해 제어한다. 각 날개에 대해, Wing

Fence의 유무를 비교한다. 4. Cyclodial Propeller Optimize.

4-1 : 3번 실험에서 얻은 데이터를 바탕으로, 최적화된 Cyclodial Propeller를 유속과 유속의 방향을 바꾸어가며 테스트한다. 각 실험, 구체적인 내용.

### 0. Test Stand Verification 0-1 : RPM Meter

RPM Meter를 IR 거리 센서와 Arduino를 이용하여 만들 계획. RPM Meter 기준 RPM을 RPM_Test, 영상 분석 (1초/240fps) 기준 RPM을 RPM_Real

로 한다. 이때, RPM_Test 기준 500, 1000, 1500 RPM으로 회전하는 회전체를 구성한다. 각 RPM에 대해서 240fps 영상을 찍어 직접 회전수를 확인한다. 오차를 분석한다. 0-2 : Thrust

Thrust를 g 단위로 분석할 예정. 힘점에 무게추를 놓고 실제 값과 측정값의 오차를

### 비교한다. 1. 기본 프로펠러 분석

1-1 : 프로펠러를 정지한 유체 속에서 가동시키면서 RPM (회전수), Thrust, 소음, Power를 측정한다.

[실험 방법] :

프로펠러를 정지한 유체 속에서, Propeller Test Stand에 Mount 시킨 이후, Power Level을 천천히 올리면서 RPM, Thrust, 소음을 주어진 기구로 측정한다.

[실험 도구] :

- MT2212 (Motor) - Propeller (기본 제공 프로펠러)

[TEST STAND – Default Propeller Version]


그림 1 : Single Axis Load Cell Propeller Test Stand.

[목표 데이터] :

Power에 대한 RPM, Thrust, 소음

[데이터 분석으로 얻고자 하는 것] :


프로펠러의 특징, 장점과 단점을 Cyclodial Propeller와 대조하기 위함. 기대되는 특징으로는 고RPM에서 높은 효율을 가지며, 무게에 비해 높은

추력성능을 가진다는 점이다.

[추출할 지표] :

Thrust-Power, Thrust-RPM, Thrust-DB Graph 추출. Thrust/Power [g/W] - 소요된 Power에 대한 Thrust. 전반적인 추력 효율을

나타낸다고 볼 수 있다. Thrust/Power 가 최대가 되는 지점에서의 dB와 RPM을 구한다. 2. 기본 Cyclodial Propeller 분석

### 2-1 : Default Cyclodial Propeller를 다양한 유속과 각도 속에서

가동시키면서 RPM (회전수), Thrust, 소음, Power를 측정한다.

[실험 방법] :

Cyclodial Propeller를 풍동실 속에서, Test Stand에 Mount 시킨 이후, Power Level을 천천히 올리면서 RPM, Thrust, 소음을 주어진 기구로 측정한다. 이때 풍동실의 외부 유속과 각도를 바꾸어 가며 Test 한다.

[실험 도구] : - Cyclodial Propeller


[TEST STAND]
[목표 데이터] :

Power에 대한 RPM, Thrust, 소음
[데이터 분석으로 얻고자 하는 것] :


Default Cyclodial의 특징, 장점과 단점을 Propeller와 대조하기 위함. Wing Fence를 장착함으로써 얻을 수 있는 이점들을 더욱 분명하게 대조하기

위해서 실험을 한다.

[추출할 지표] :

Thrust-Power, Thrust-RPM, Thrust-DB Graph 추출. Thrust/Power [g/W] - 소요된 Power에 대한 Thrust. 전반적인 추력 효율을

나타낸다고 볼 수 있다. Thrust/Power 가 최대가 되는 지점에서의 dB와 RPM을 구한다. 바람의 유속과 Cyclodial Propeller가 이루는 각을 theta 라고 두자. 각 theta와

유속에 대해서, Maximum Thrust/W 그래프를 3차원상에서 나타낸다. 이때 예상되는 결과는 theta가 0에 근접할 때 커지는 것이다. 따라서, WingFence 구조를 도입하여 성능을 증가시키는 것이 이 실험의

### 목적이다. 2-2 : Relative Curvature를 적용한 회전체와 그렇지 못한 회전체의 RPM

감쇠 속도를 비교한다.

[실험 방법] :

특정 RPM까지 Cyclodial Propeller를 가속 시킨 이후, Relative Curvature 적용된 모델과 그렇지 못한 모델의 RPM 감소 속도를 대조한다.

[실험 도구] :

실험군 : 기본 Straight Flap 회전체
대조군 : Curvature Flap 회전체
Motor & RPM Stand. (기존 Test Stand 사용 가능)

[목표 데이터] :

실험군과 대조군이 정지하는데까지 걸리는 시간. 실험군과 대조군의 회전 관성.

[데이터 분석으로 얻고자 하는 것] :

Curvature Flap의 Drag Level이 Straight Flap의 Drag Level보다 적다. 따라서, 정지하는데까지 걸리는 시간은 Curvature Flap이 더 길다. 3. Flap (Wing Fence) 분석

3-1 : Flap Analysis.

[실험 방법] :

각 날개를 풍동실에 넣어, 유속, 회전각, 받음각을 변수로 하여 테스트한다. 이때, 회전각과 받음각, 유속은 자동화된 실험장치를 이용해 제어한다. 각 날개에 대해, Wing Fence의 유무를 비교한다. 이때, 날개의 구조와 Wing Fence의 구조는 다양한 항공 논문을 참고하여

제작한다.

[실험 도구] :

Flap Test Stand.
다양한 Flap.

[목표 데이터] :

Flap별 유속과 받음각, 각도에 따른 Fz와 Fy.

[데이터 분석으로 얻고자 하는 것] :

Flap의 Wing Fence 유무와 종류에 따른 차이. 최대 Lifting Force와 Drag, 유속에 따른 Flow Separature Angle.

4. Cyclodial Propeller Optimize.

### 4-1 : 3번 실험에서 얻은 데이터를 바탕으로, 최적화된 Cyclodial

Propeller를 유속과 유속의 방향을 바꾸어가며 테스트한다.

[실험 방법] :

3번 실험의 데이터를 기반으로, - 가장 작은 Drag을 나타낸 Flap

- 가장 큰 Flow Separature Angle을 나타낸 Flap
- Flow Separature Angle/ Drag이 가장 큰 Flap
- Thrust/Drag 이 가장 큰 Flap
이렇게 4가지 Flap을 바탕으로 하여 Optimized Cyclodial Propeller를 만들어 성능을 기존 Default Cyclodial Propeller와 비교한다.

[실험 도구] :

Cyclodial Propeller Test Stand 4가지 Cyclodial Propeller.

[목표 데이터] :

Cyc Propeller별 유속과 각도, Power에 따른 Fz와 Fy.

[데이터 분석으로 얻고자 하는 것] :

1. 정지한 상태에서의 Maximum Thrust/Power
2. 유속의 방향이 바뀔 때 Thrust Variance
3. Maximum Thrust에서의 dB
4. Maximum Thrust/Power 에서의 dB
- 기존 Propeller보다 조용하다. - 기존 Propeller보다 높은 Thrust/Power 를 가진다. - 기존 Cyclodial Propeller 에 비해 Thrust Variance가 작다. - 기존 Cyclodial Propeller에 비해 높은 Maximum Thrust/Power를 가진다.

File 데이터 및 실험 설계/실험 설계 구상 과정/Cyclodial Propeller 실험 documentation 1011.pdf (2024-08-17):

[Cyclodial Propeller Airfoil 선정]

목차 :
파괴되기 전의 RPM, Cyclodial Propeller의 적당한 속도. 기본형 Cyclodial Propeller 에 대해 측정한 데이터를 바탕으로 알아내야 할 듯 함.

[1차 실험 : Straightflap CYC test] :
RPM을 점차 올려가면서, 파괴되기까지 RPM을 상승시킨다. 이때 RPM과 Thrust를 측정한다. RPM과 Thrust에서 적당한 영역에서의 날개 접선 속도를 계산하고 이를 향후 날개 적

용에 대입한다. 접선 속도를 구하였다면, 다음 단계인 레이놀즈 수를 구하여야 함. http://airfoiltools.com/calculator/reynoldsnumber

레이놀즈 수는 씨발 무엇인가

[2차 실험 : Relative Curvature] :
Relative Curvature Remapping Algorithm :
1. No Remapping
2. Center-Chord British Convention Remapping
3. Center-Camber American Standard Remapping
둘 중에서 가장 예측한 것과 유사하게 나오는 Remapping Algorithm 이 맞는거임. 예측해야 할 것 :

속도에 따른 Thrust 특성. 모든 각에서의 Pitch Angle을 알 수 있으므로 대충 모든 RPM에서 Thrust 또한 예

측이 가능하다. 이를 계산해서 대조해 볼 것

Stall RPM

이렇게 해서 선정된 Flap 에 대해서, 다음 단계인 Wing Fence를 적용하게 된다.

[3차 실험 : Wing Fence 적용 at Airfoils]

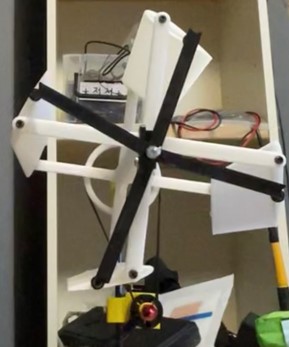
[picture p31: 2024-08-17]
Media/그림5.jpg

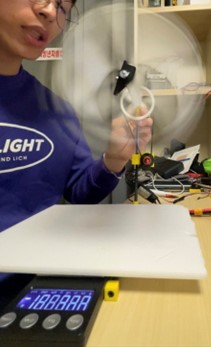
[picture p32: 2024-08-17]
Media/그림6.jpg

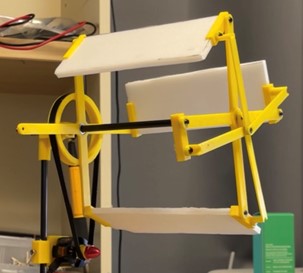
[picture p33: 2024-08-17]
Media/그림4.jpg

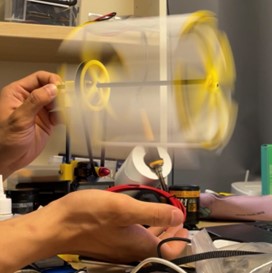
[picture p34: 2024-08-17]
Media/그림3.jpg

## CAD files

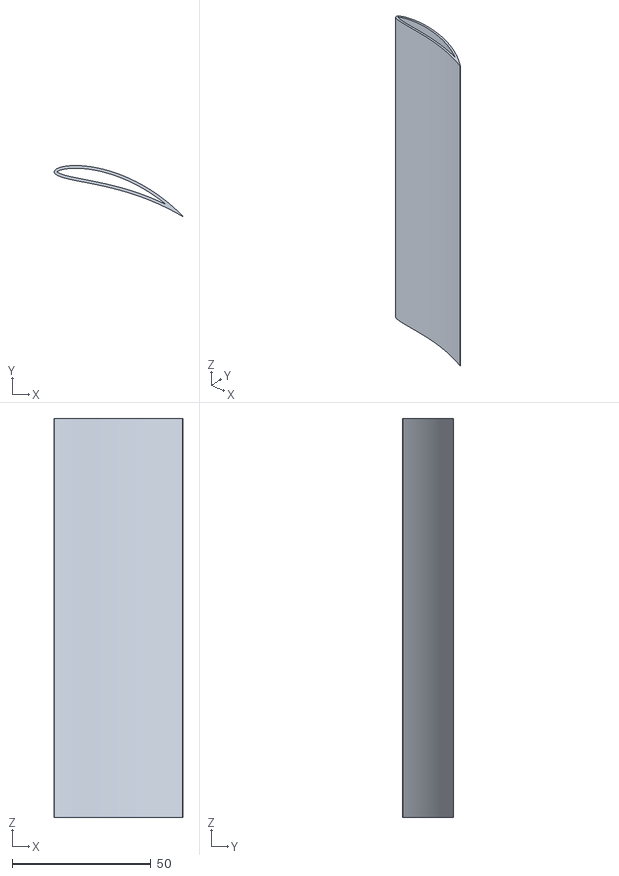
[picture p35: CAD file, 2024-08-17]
BUILD/V2_V3_BUILD/0012/Curved Main/Curved Main 144mm.stl
46.4 x 18.4 x 144.0

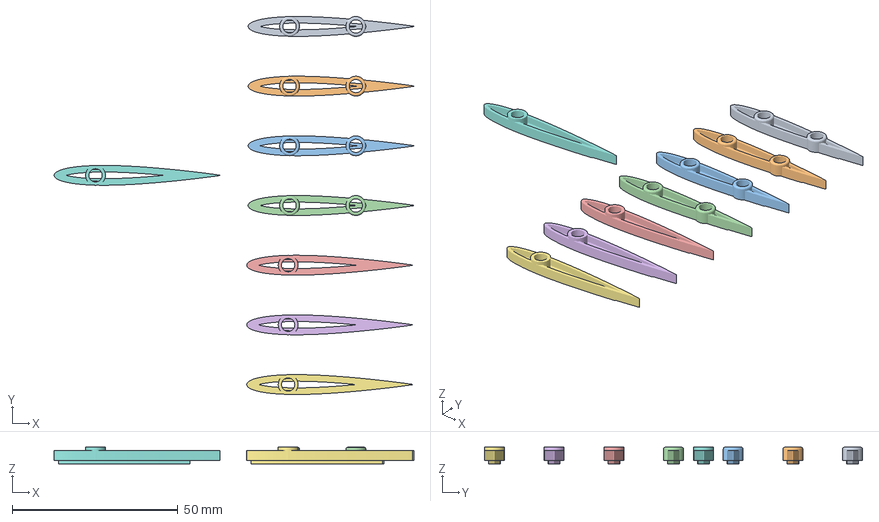
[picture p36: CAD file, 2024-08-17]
BUILD/V2_V3_BUILD/0012/Not Curved Main/Not Curved Main 144mm.3mf
108.5 x 114.0 x 5.00 mm
L.stl x 4
R.stl x 4

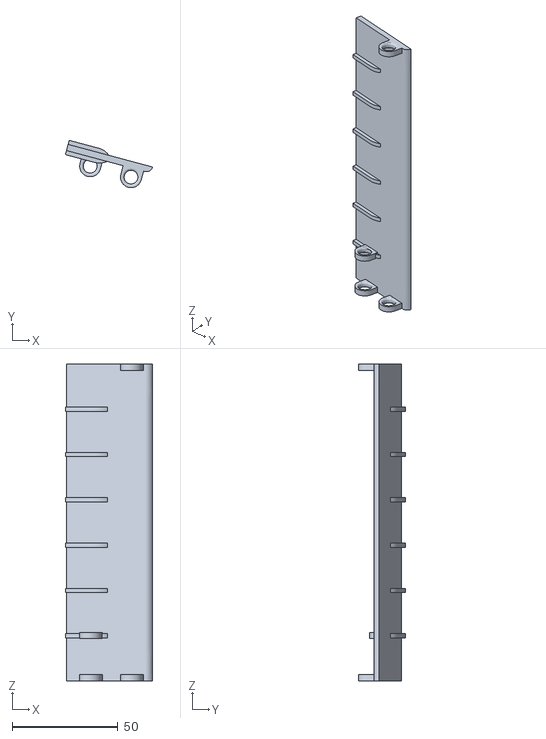
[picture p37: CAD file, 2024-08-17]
BUILD/V0_V1_BUILD/StraightFlapWF.stl
41.3 x 22.4 x 150.0

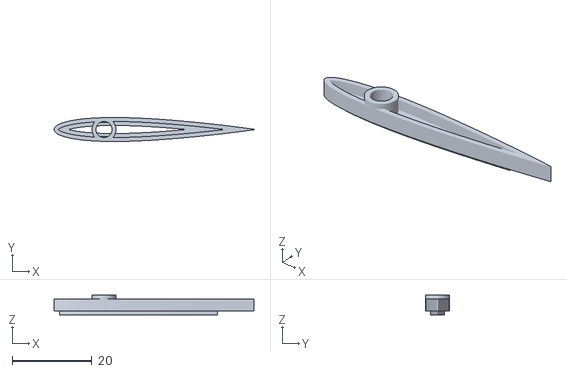
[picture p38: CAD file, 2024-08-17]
BUILD/V2_V3_BUILD/0012/Not Curved Main/R.stl
50.0 x 6.00 x 5.00

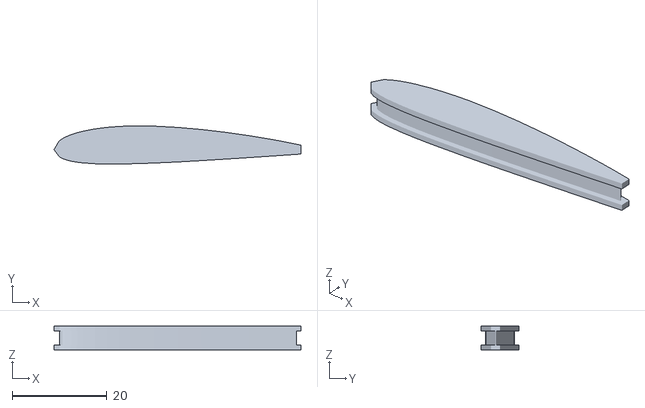
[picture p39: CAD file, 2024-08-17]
BUILD/V2_V3_BUILD/2412/nichromewire_bendframe.stl
52.2 x 8.06 x 5.00

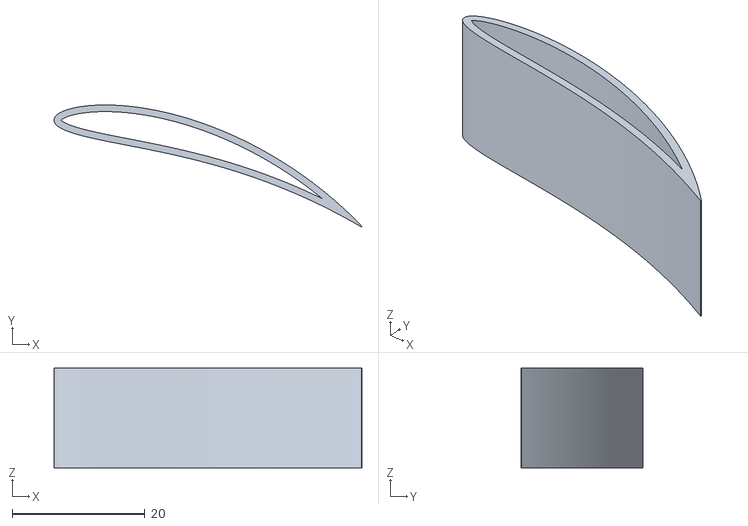
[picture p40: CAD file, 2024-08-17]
BUILD/V2_V3_BUILD/Calibrate LW pla/Curved tst 15mm.stl
46.4 x 18.4 x 15.0

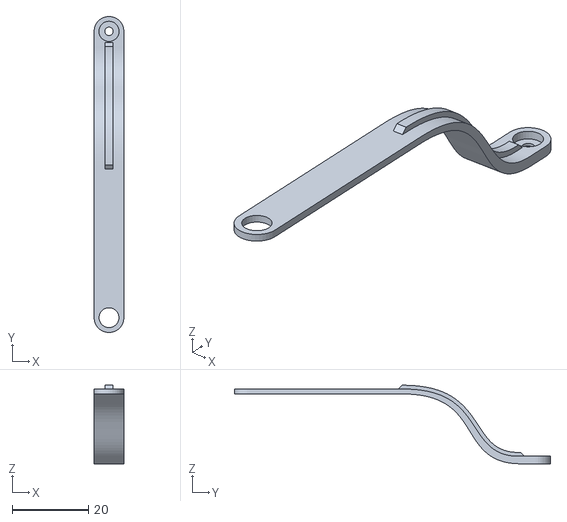
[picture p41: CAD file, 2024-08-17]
BUILD/V2_V3_BUILD/Curved and gilled Flaparm/n2.stl
7.80 x 82.8 x 20.6

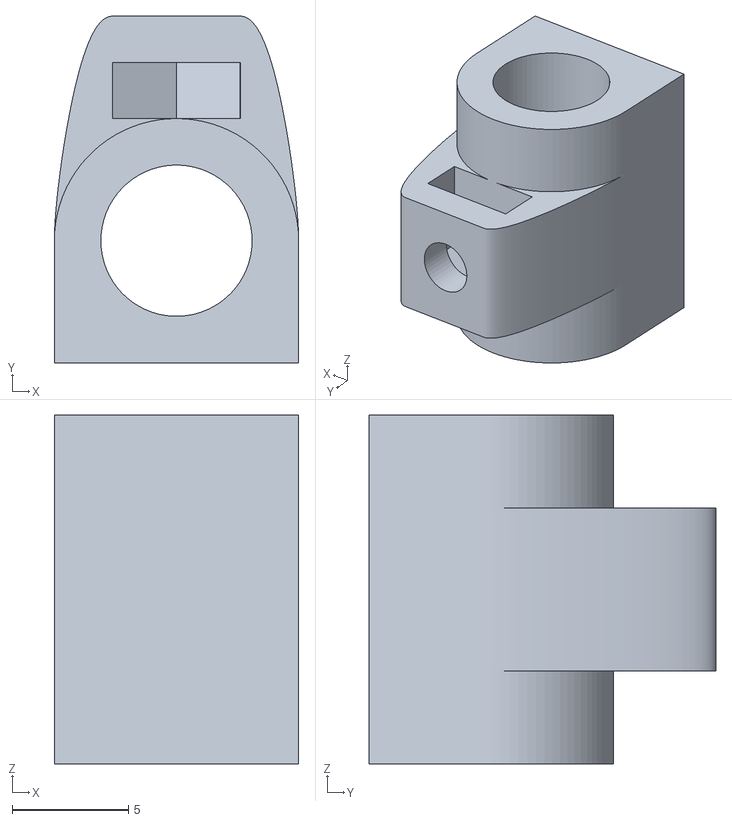
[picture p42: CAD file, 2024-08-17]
BUILD/V2_V3_BUILD/Thrust Stand/foot.stl
10.5 x 14.9 x 15.0

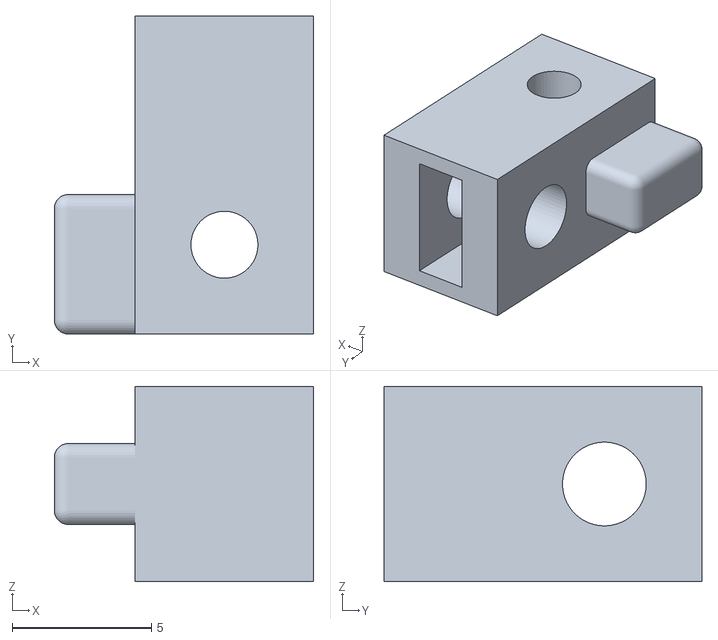
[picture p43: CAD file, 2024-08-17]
BUILD/V2_V3_BUILD/VARIABLE PITCHER 6MM/B.stl
9.30 x 11.4 x 7.00

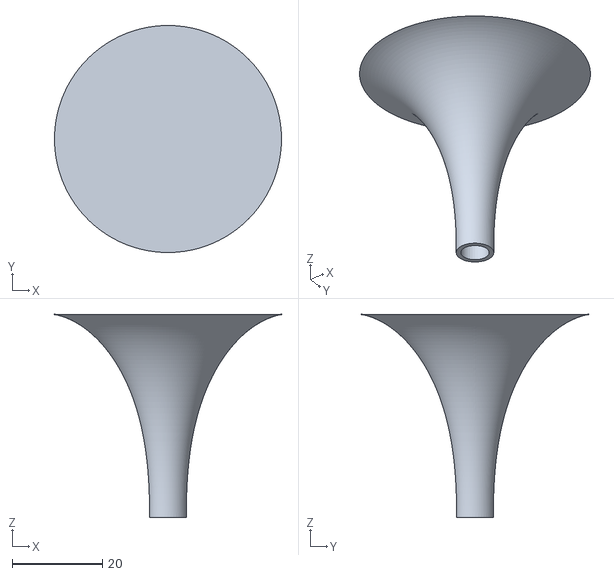
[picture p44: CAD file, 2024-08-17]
대회 출전 Documentation/V3_KSEF CYC/Showcase_쇼케이스 준비/build/weight holder on top.stl
50.3 x 50.3 x 45.0

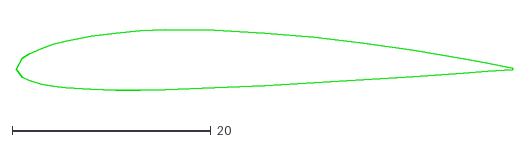
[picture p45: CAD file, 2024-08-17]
데이터 및 실험 설계/Codes/airfoil dxf/naca2412 chord 50.dxf
50.0 x 6.05

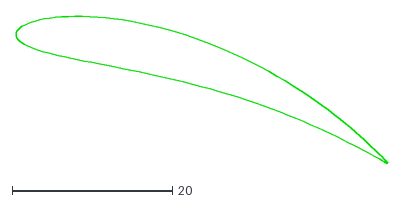
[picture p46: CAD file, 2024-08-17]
데이터 및 실험 설계/Codes/CurvedAirfoildxf/output_1.dxf
46.4 x 18.4

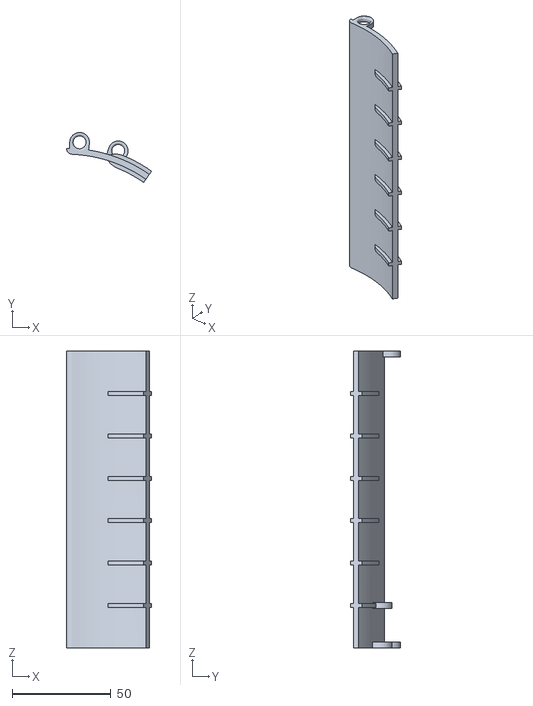
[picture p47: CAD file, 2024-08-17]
BUILD/V0_V1_BUILD/roundflapWF.stl
43.0 x 25.3 x 150.0

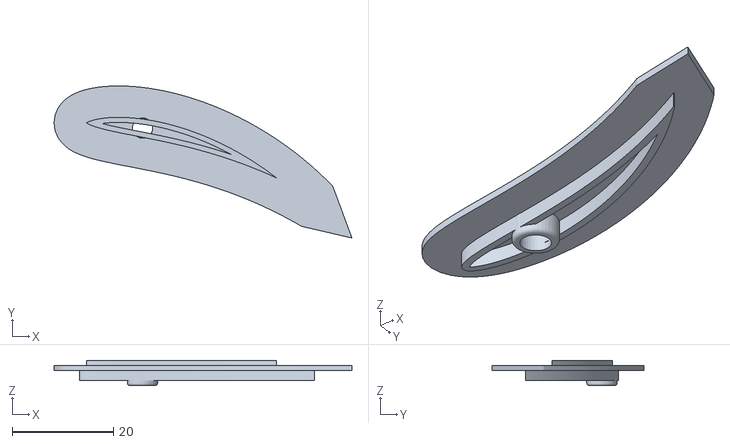
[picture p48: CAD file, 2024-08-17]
BUILD/V2_V3_BUILD/0012/Curved Main/R WF.stl
58.8 x 30.0 x 5.00

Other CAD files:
BUILD/V2_V3_BUILD/2412/2412 cutter hot wire.stl
BUILD/V2_V3_BUILD/Curved and gilled Flaparm/nn4.stl
BUILD/V2_V3_BUILD/Thrust Stand/중심고정부.stl
BUILD/V0_V1_BUILD/StraightFlap1.stl
BUILD/V0_V1_BUILD/roundflap1.stl
BUILD/V2_V3_BUILD/0012/Curved Main/L WF.stl
BUILD/V2_V3_BUILD/0012/Curved Main/L.stl
BUILD/V2_V3_BUILD/0012/Curved Main/R.stl
BUILD/V2_V3_BUILD/0012/Not Curved Main/L WF.stl
BUILD/V2_V3_BUILD/0012/Not Curved Main/L.stl
BUILD/V2_V3_BUILD/0012/Not Curved Main/Not Curved Main 144mm.stl
BUILD/V2_V3_BUILD/0012/Not Curved Main/R WF.stl
BUILD/V2_V3_BUILD/Curved and gilled Flaparm/n1.stl
BUILD/V2_V3_BUILD/Curved and gilled Flaparm/n3.stl
BUILD/V2_V3_BUILD/Curved and gilled Flaparm/n4.stl
BUILD/V2_V3_BUILD/Curved and gilled Flaparm/nn1.stl
BUILD/V2_V3_BUILD/Curved and gilled Flaparm/nn2.stl
BUILD/V2_V3_BUILD/Curved and gilled Flaparm/nn3.stl
BUILD/V2_V3_BUILD/Thrust Stand/erect.stl
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

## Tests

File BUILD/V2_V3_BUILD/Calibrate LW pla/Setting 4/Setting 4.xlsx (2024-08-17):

Nice Vase Mode Print
Print Settings |  | Filament Settings
Layer Height | 0.3 | Flow Rate | 0.45
Line Width (ALL) | 0.6 | Temp | 260
Speed (All) | 20
Spiral Vase | O

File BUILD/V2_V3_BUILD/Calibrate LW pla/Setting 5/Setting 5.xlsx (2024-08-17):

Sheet: Settings
Nice Vase Mode Print | Thicker
Print Settings |  | Filament Settings
Layer Height | 0.3 | Flow Rate | 0.45
Line Width (ALL) | 0.8 | Temp | 260
Speed (All) | 20
Spiral Vase | O

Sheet: Printout Evaluation
Preset Weight | Printout Weight
2.7 | 5.1
 | Why!!
 | 1 | 기입된 밀도가 이상하다 | (문제 없음)
 | 2 | 너무 높은 Flow Rate로 더 넓어진다 | Flow Rate 감소
 | 3 | 노즐 속도가 너무 빨라 팽창하지 못한다 | 노즐 속도 감소, Flow Rate 감소
 | 4 | 온도가 너무 낮다
 | 경량화 방법
 | 1 | Layer Width 감소
 | 2 | Flow Rate 감소

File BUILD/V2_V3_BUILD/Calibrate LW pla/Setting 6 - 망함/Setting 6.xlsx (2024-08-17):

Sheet: Settings
Nice Vase Mode Print | Thicker
Print Settings |  | Filament Settings
Layer Height | 0.4 | Flow Rate | 0.45
Line Width (ALL) | 0.8 | Temp | 260
Speed (All) | 20
Spiral Vase | O

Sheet: Printout Evaluation
망함
거품 형태로 뽀글거리게 나오고 층간 결합이 안됨
0.4mm 노즐로 0.4 Layer Height 하니까 전혀 안눌려서 그런듯

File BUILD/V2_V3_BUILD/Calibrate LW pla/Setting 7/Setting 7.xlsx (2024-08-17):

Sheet: Settings
Nice Vase Mode Print | Thicker
Print Settings |  | Filament Settings
Layer Height | 0.3 | Flow Rate | 0.4
Line Width (ALL) | 0.8 | Temp | 260
Speed (All) | 20
Spiral Vase | O

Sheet: Printout Evaluation
EST Curved Model 144mm | 5.3
Real Curved Model 144mm | 5.1 | 96.22641509%

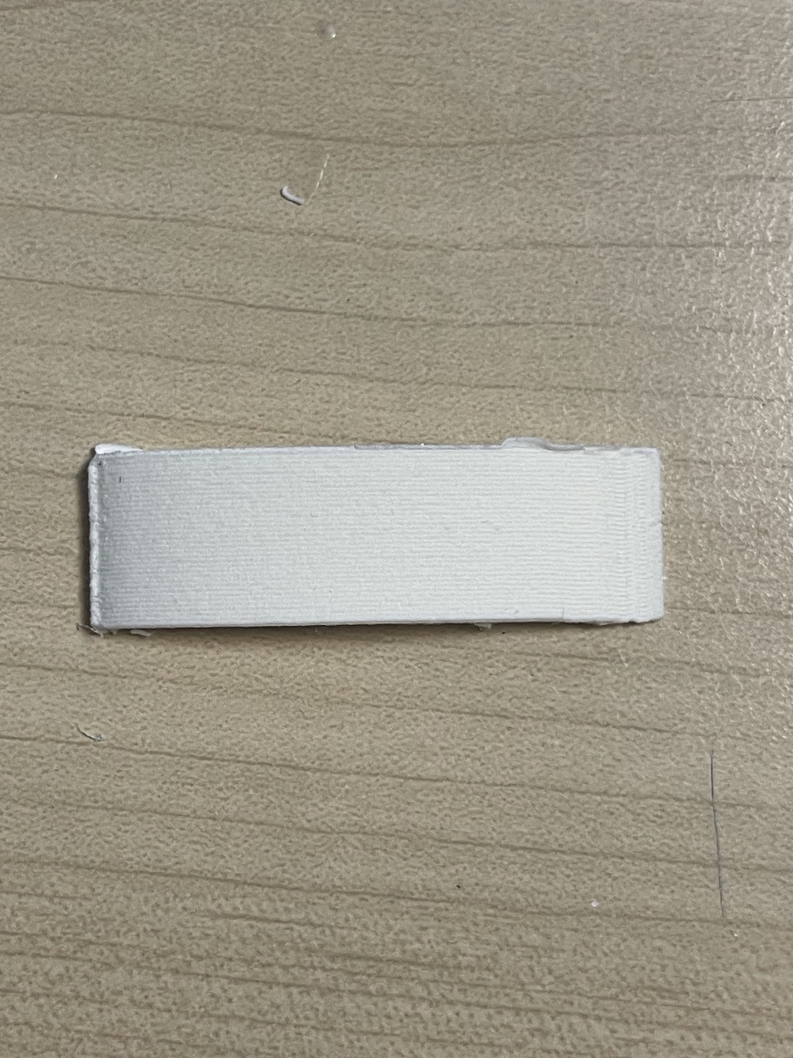
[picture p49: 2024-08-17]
BUILD/V2_V3_BUILD/Calibrate LW pla/Setting 1/KakaoTalk_20231118_113036356_03.jpg

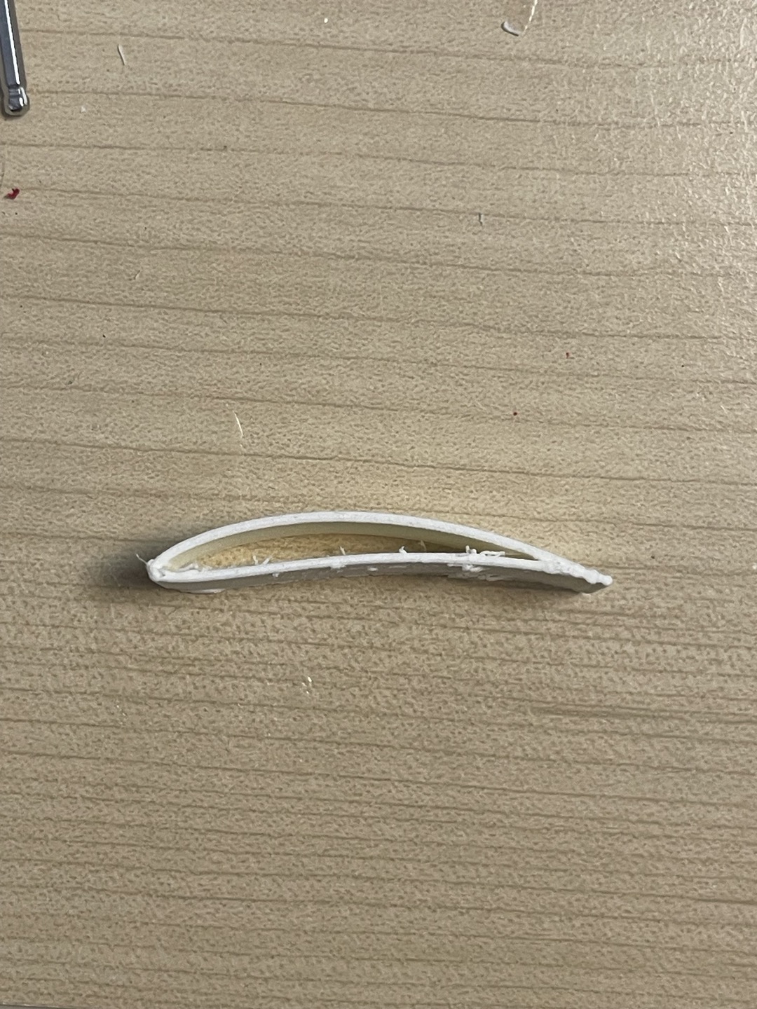
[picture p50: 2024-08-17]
BUILD/V2_V3_BUILD/Calibrate LW pla/Setting 1/KakaoTalk_20231118_113036356_02.jpg

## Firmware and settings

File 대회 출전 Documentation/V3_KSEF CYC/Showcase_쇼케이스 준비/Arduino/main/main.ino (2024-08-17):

#include <Servo.h>
#include "HX711.h"

// Servos for each propeller
Servo servoA, servoB, servoC;

// Tachometers variables
unsigned long rpmTimeA, rpmTimeB, rpmTimeC;
bool tooSlowA = true, tooSlowB = true, tooSlowC = true;

// Load Cells
HX711 loadCellA, loadCellC;
long weightA, weightB, weightC;

// Load Cell calibration and pins
long zeroA, zeroB, zeroC;
long calFactorA, calFactorB, calFactorC;
const int LOADCELL_DOUT_PIN_A = 5; // Modify these pins as per your hardware setup
const int LOADCELL_SCK_PIN_A = 6;
const int LOADCELL_DOUT_PIN_C = 7; // Modify these pins as per your hardware setup
const int LOADCELL_SCK_PIN_C = 8;

int rpmA, rpmB, rpmC;
// Repeat for loadCellB and loadCellC with different pins

void setup() {
  Serial.begin(115200);

  // Setup Servos
  servoA.attach(9); // Modify these pins as per your hardware setup
  servoB.attach(10);
  servoC.attach(11);

  // Setup Load Cells
  loadCellA.begin(LOADCELL_DOUT_PIN_A, LOADCELL_SCK_PIN_A);
  loadCellC.begin(LOADCELL_DOUT_PIN_C, LOADCELL_SCK_PIN_C);

  // Repeat setup for loadCellB and loadCellC with their respective pins

  // Setup Tachometers
  pinMode(2, INPUT); // Modify these pins as per your hardware setup
  pinMode(3, INPUT);
  pinMode(18, INPUT);
  
  attachInterrupt(digitalPinToInterrupt(2), RPM_A, FALLING);
  attachInterrupt(digitalPinToInterrupt(3), RPM_B, FALLING);
  attachInterrupt(digitalPinToInterrupt(18), RPM_C, FALLING);

  // Initialize Timers for Tachometers
  TCCR3A = 0; TCCR3B = 0b00000100; TIMSK3 = 0b00000001; // Timer 3
  TCCR4A = 0; TCCR4B = 0b00000100; TIMSK4 = 0b00000001; // Timer 4
  TCCR5A = 0; TCCR5B = 0b00000100; TIMSK5 = 0b00000001; // Timer 5
}

void loop() {
  if (Serial.available()) {
    int powerA, powerB, powerC;
    sscanf(Serial.readStringUntil('\n').c_str(), "%d %d %d", &powerA, &powerB, &powerC);
    servoA.write(map(powerA, 0, 100, 0, 180));
    servoB.write(map(powerB, 0, 100, 0, 180));
    servoC.write(map(powerC, 0, 100, 0, 180));
  }

  // Read and store weight from each load cell
  weightA = readWeight(loadCellA, calFactorA, zeroA);
  weightB = weightA;
  weightC = readWeight(loadCellC, calFactorC, zeroC);
  if (!tooSlowA) {
    rpmA = calculateRPM(rpmTimeA);
    Serial.print("RPM A: ");
    Serial.println(rpmA);
  }
  if (!tooSlowB) {
    rpmB = calculateRPM(rpmTimeB);
    Serial.print("RPM B: ");
    Serial.println(rpmB);
  }
  if (!tooSlowC) {
    rpmC = calculateRPM(rpmTimeC);
    Serial.print("RPM C: ");
    Serial.println(rpmC);
  }
  Serial.print("A ");
  Serial.print(rpmA);
  Serial.print(' ');
  Serial.print(weightA);
  Serial.print('_');
  Serial.print("B ");
  Serial.print(rpmB);
  Serial.print(' ');
  Serial.print(weightB);
  Serial.print('_');
  Serial.print("C ");
  Serial.print(rpmC);
  Serial.print(' ');
  Serial.print(weightC);
}

long readWeight(HX711 &loadCell, long calFactor, long zero) {
  if (loadCell.is_ready()) {
    long reading = loadCell.read();
    return (reading - zero) / calFactor;
  } else {
    return 0; // Error value
  }
}

float calculateRPM(unsigned long timerCount) {
  float rpmFloat = 60.0 * (16000000.0 / 256.0) / timerCount;
  return round(rpmFloat);
}

ISR(TIMER3_OVF_vect) { tooSlowA = true; }
ISR(TIMER4_OVF_vect) { tooSlowB = true; }
ISR(TIMER5_OVF_vect) { tooSlowC = true; }

void RPM_A() { rpmTimeA = TCNT3; TCNT3 = 0; tooSlowA = false; }
void RPM_B() { rpmTimeB = TCNT4; TCNT4 = 0; tooSlowB = false; }
void RPM_C() { rpmTimeC = TCNT5; TCNT5 = 0; tooSlowC = false; }

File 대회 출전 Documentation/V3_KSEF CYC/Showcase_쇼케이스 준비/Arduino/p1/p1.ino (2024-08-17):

#include <Servo.h>
#include "HX711.h"


//setting Servo
Servo ESC;

//Setting Tacho
unsigned long rpmtime;
float rpmfloat;
unsigned int rpm;
bool tooslow = 1;

const int INTERRUPT_SENSOR_PIN = 2;

//Setting LoadCell
const int LOADCELL_DOUT_PIN = 5;
const int LOADCELL_SCK_PIN = 6;
HX711 scale;
int powerLevel;

long zero = 1286527;
long _500g = 2136588;
long weight = 0;

bool test_mode = false;

void setup() {
  Serial.begin(9600); // Initialize the serial communication at 9600 baud rate
  TCCR3A = 0; //Named as Timer/Counter Control Register
  TCCR3B = 0b00000100; //Prescaler 256
  TIMSK3 = 0b00000001; //enable timer overflow
  
  ESC.attach(9);
  pinMode(2, INPUT);

  scale.begin(LOADCELL_DOUT_PIN, LOADCELL_SCK_PIN);
  attachInterrupt(digitalPinToInterrupt(INTERRUPT_SENSOR_PIN), RPM, FALLING);
  //digitalPinToInterrupt(INTERRUPT_SENSOR_PIN)
}



void loop() {
  
  float cal_factor = (_500g-zero)/509;
  
  if (Serial.available()) { // Check if data is available to read
    powerLevel = Serial.parseInt(); // Parse the incoming integer value
  }
  
  int thrusttoservo = map(0, 100, 62, 70, powerLevel);
  
  ESC.write(thrusttoservo);
    
  delay(1000);
  if (tooslow == 1) {
    Serial.print("-1");
  }
  else {
    rpmfloat = 60 / (rpmtime/ float((16000000/256)));
    rpm = round(rpmfloat);
    Serial.print(rpm/4);
  }
  Serial.print(" ");
  if (scale.is_ready()) {
    long reading = scale.read();
    Serial.print((reading-zero)/cal_factor);
  } 

  Serial.println();
}


ISR(TIMER3_OVF_vect) {
  tooslow = 1;
}
void RPM () {
  rpmtime = TCNT3;
  TCNT3 = 0;
  tooslow = 0;
}

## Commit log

2024-08-17 전체 업뎃
    [0012 Curved NO WF.xlsx, 0012 Curved WF.xlsx, 0012 LW one.3mf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]
2024-08-18 realproptest vid 추가
